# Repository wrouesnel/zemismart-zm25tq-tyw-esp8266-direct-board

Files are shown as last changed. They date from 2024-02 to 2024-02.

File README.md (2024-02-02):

# ESP8266 Adapter Board for Zemismart ZM25TQ-TYW Tubular Motor

This is a PCB I designed for doing an ESP chip swap on the Zemismart ZM25TQ-TYW tubular motor.

It allows a simple direct replacement of the WBR1 microcontroller board, which rides on a carrier shim to
mate with the motorized blind itself. Communication happens over serial using the Tuya protocol, so ESPHome
can speak to it easily.

The carrier board in the motor tube is marked `TYWBR1_VER 0.0 210131`. The PCB in this repository is
designed to be a direct replacement for it, carrying an ESP-07 or ESP-07S (ESP-07S recommended).

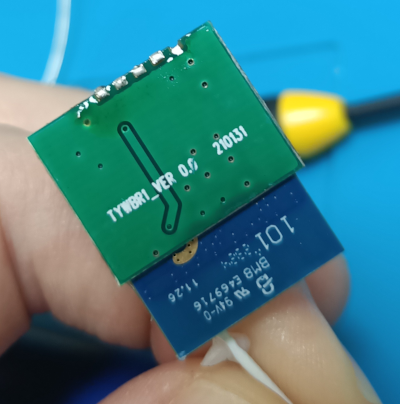
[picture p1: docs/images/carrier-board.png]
Carrier Board


You want to use the ESP-07 series because of the on-board SMA connector, which allows using the included antenna
with the tubular motor directly. You need to remove a 0 ohm resistor from these boards to use the external antenna.

The resistor to remove is shown below - the pads closest to the chip.

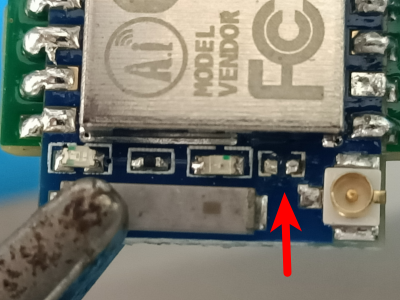
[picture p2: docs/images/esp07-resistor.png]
Desoldered Resistor


## Production

The [JLCPCB production files](jlcbpcb/production_files) I used for this board are included, use the SMD single-sided assembly service - all parts
are basic resistors which costs cents for assembly.

One consideration with production was I used the default PCB thickness - this worked fine, but a thinner PCB might
be better since castellate solder pads cost considerably more - and a little less height will help with the workaround
for soldering.

## Usage

**NOTE**: these instructions assume you know what you are doing. If this all seems to daunting, please don't plough
ahead anyway.

Make sure you flash your ESP with ESPHome before assembling everything! How to do this is described well elsewhere.
The ESPHome configuration to set the motor up as a [generic blind](esphome/generic-zemismart-zm25tq-tyw.yaml) is here.
I recommend customizing it for your use case (namely: set it up to auto-connect to your wifi, I've also added a required
secret for the fallback-wifi-password - you don't want that to default to open).

The motor comes apart fairly easily - just undo the screws (the design seems to have improved since the first one
I bought which required more force). I did have to desolder the reset switch to get it out. Take pictures while
you disassemble so you can re-assemble.

The image below shows the two boards side by side sitting on top of the blind motor board.

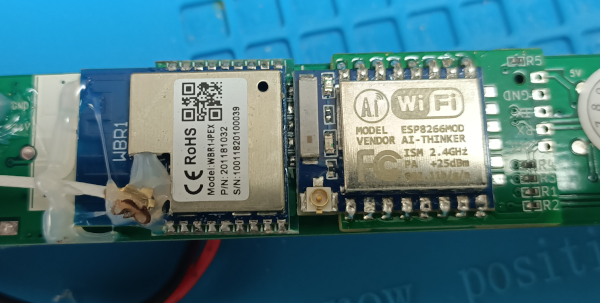
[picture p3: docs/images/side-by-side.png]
Side-By-Side


The easiest way to desolder this board is to add more solder to bridge all the pads, then use the soldering iron to
heat the blob up to liquid. There's tape underneath the chip, so use a small screw-driver to get the board up. Make
sure the solder is melted though - the traces underneath are fragile and can get lifted doing this (though there are
ways to repair it).

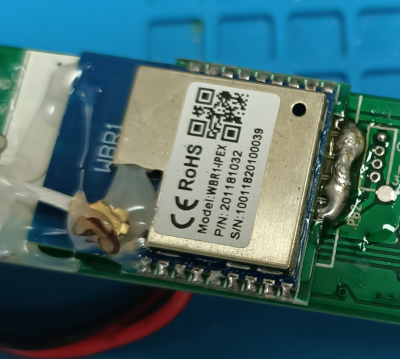
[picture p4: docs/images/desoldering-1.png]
Desoldering


Showing the chip and the tape...

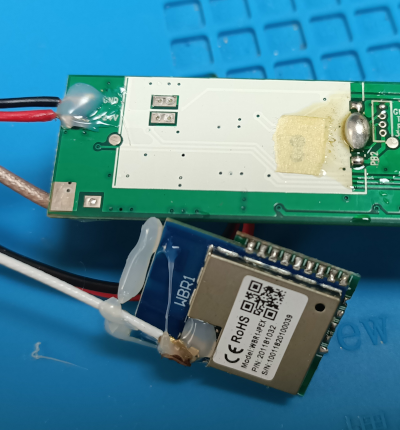
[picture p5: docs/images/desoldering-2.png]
Desoldered


Use a desoldering gun or some solder wick to clean up the pads. I have a cheap desoldering station which works great.

I put red electrical tape over the white section of the mask to cover the test pads - these have 24V when the motor
is powered, so it's just some extra insulation.

The PCB doesn't have castellate pads - they add a considerable premium. The two possible solutions are to file the pads
on the edge till the open up, or to do a kind of careful solder bridge over the edge. I opted for the latter, but it
is is tricky - try what works best (I'll try the pseudo-castellation next time round).

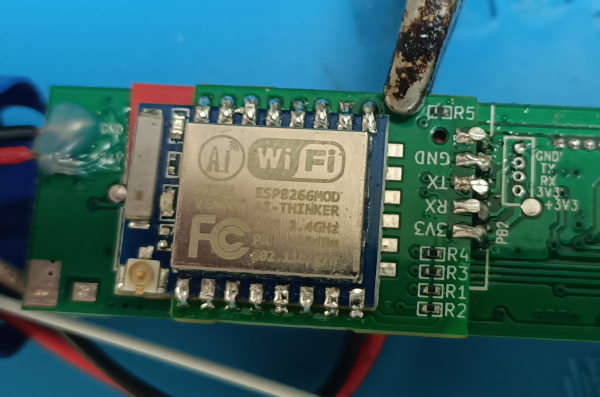
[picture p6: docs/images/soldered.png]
Soldered


The original PCB is hot glued down to provide support. I used electrical tape to cover the pseudo-castellations and the
top of the IPEX antenna. The final product looks like this, and fits back in the tube nicely.

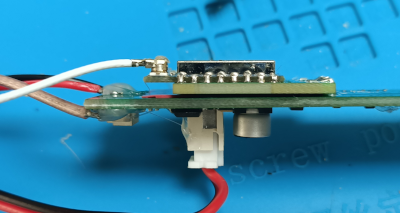
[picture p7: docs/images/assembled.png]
Assembled


And taped up:

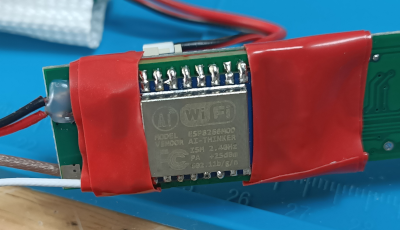
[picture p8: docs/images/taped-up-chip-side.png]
Chip Side
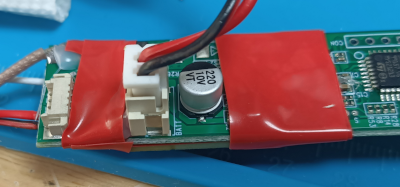
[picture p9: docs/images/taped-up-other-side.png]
Other Side
 

When it's all back together, it's seamless - but maybe put a label on it so you know it's been chip-swapped (also
which specifies the name of the chip you put in - there's a lot of options you could go with).

### Will it work elsewhere?

Probably! I suspect this carrier board is pretty common. The Zemismart motor design has been improved and disassembled
quite well, so having the carrier board in hand made swapping it out a breeze.

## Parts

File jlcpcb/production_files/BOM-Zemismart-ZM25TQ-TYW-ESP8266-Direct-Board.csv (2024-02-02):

Comment | Designator | Footprint | LCSC
10K | R1,R2,R3,R4,R5 | R0402 | C25744

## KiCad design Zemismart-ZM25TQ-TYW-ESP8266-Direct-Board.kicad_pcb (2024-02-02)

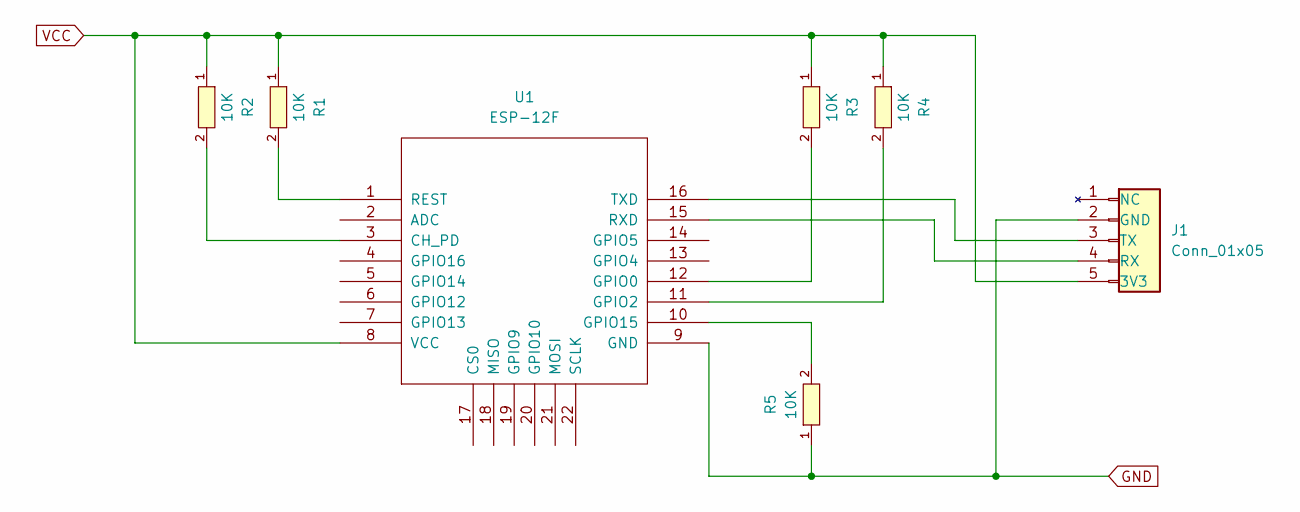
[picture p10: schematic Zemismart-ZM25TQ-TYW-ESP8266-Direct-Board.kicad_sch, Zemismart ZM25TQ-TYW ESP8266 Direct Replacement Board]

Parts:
J1: Conn_01x05; JST_PH_B5B-PH-K_1x05_P2.00mm_Vertical
R1, R2, R3, R4, R5: 10K; R0402; LCSC C25744
U1: ESP-12F; ESP-12E_SMD

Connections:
GND: J1.2 (GND), R5.1, U1.9 (GND)
unnamed: J1.4 (RX), U1.15 (RXD)
unnamed: J1.3 (TX), U1.16 (TXD)
unnamed: R2.2, U1.3 (CH_PD)
unnamed: R3.2, U1.12 (GPIO0)
unnamed: R4.2, U1.11 (GPIO2)
unnamed: R5.2, U1.10 (GPIO15)
unnamed: R1.2, U1.1 (REST)
VCC: J1.5 (3V3), R1.1, R2.1, R3.1, R4.1, U1.8 (VCC)

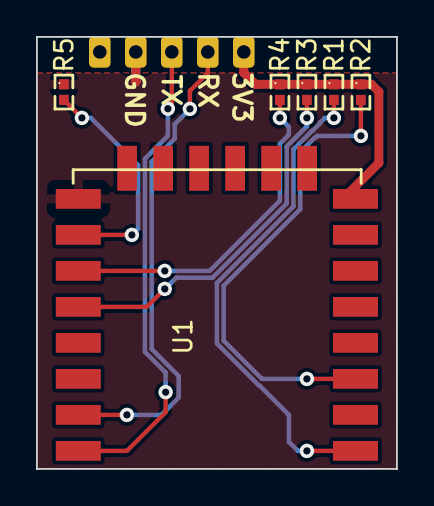
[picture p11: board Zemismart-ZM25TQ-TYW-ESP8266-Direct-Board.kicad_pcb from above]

Board: 2 copper layers, 20.0 x 24.0 mm, 7 parts (0 on the bottom side), 9 nets.

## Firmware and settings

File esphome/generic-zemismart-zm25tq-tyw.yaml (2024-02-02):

# ESP-1S chip-swapped Zemismart ZM25TQ (TY-W) motorized blinds.
# These have a WBR1-IPEX chip in them originally, communicating over
# serial. It provides 3.3V power and 3.3V TTL lines.

external_components:
- source:
    type: local
    path: components

esphome:
  name: cover-zemismart-blinds
  friendly_name: Zemismart ZM25TQ Blinds
  name_add_mac_suffix: true
  platform: ESP8266
  board: esp01_1m
  project:
    name: "wrouesnel.zemismart-zm25tq-esp01"
    version: "1.0"
  esp8266_restore_from_flash: false

logger:
  level: DEBUG
  baud_rate: 0

web_server:
  port: 80

captive_portal:

mdns:

api:

ota:

wifi:
  ap:
    password: !secret fallback_wifi_password

uart:
  tx_pin: TX
  rx_pin: RX
  baud_rate: 9600

tuya:

cover:
  - platform: tuya-ex
    name: Motor
    control_datapoint: 1
    position_datapoint: 2
    position_report_datapoint: 3
    restore_mode: NO_RESTORE
    min_value: 0
    max_value: 100
    device_class: blind
    invert_position_report: true

number:
  - platform: tuya
    name: Set Position
    min_value: 0
    max_value: 100
    step: 1
    number_datapoint: 2
    unit_of_measurement: "%"
    mode: box
    entity_category: DIAGNOSTIC

sensor:
  - platform: uptime
    name: Uptime
  - platform: wifi_signal
    name: WiFi Signal
    update_interval: 60s
    entity_category: DIAGNOSTIC
    # Sensors from Tuya
  - platform: "tuya"
    name: "Reported Position"
    sensor_datapoint: 3
    entity_category: DIAGNOSTIC
  # - platform: "tuya"
  #   name: "Setpoint Position"
  #   sensor_datapoint: 2
  #   entity_category: DIAGNOSTIC
  - platform: "tuya"
    name: "Current Operation"
    sensor_datapoint: 7
    entity_category: DIAGNOSTIC
  - platform: "tuya"
    name: "Current Situation"
    sensor_datapoint: 11
    entity_category: DIAGNOSTIC
  # Bitfield: 1 appears to mean "limits not set" - TODO: lock out the cover controls from HA
  # until limits are set.
  - platform: "tuya"
    name: "Motor Fault"
    sensor_datapoint: 12
    entity_category: DIAGNOSTIC

switch:
- platform: tuya
  name: Lower Limit Set
  switch_datapoint: 103
  entity_category: CONFIG
- platform: tuya
  name: Middle Set
  switch_datapoint: 104
  entity_category: CONFIG
- platform: tuya
  name: Upper Limit Set
  switch_datapoint: 105
  entity_category: CONFIG

select:
- platform: tuya
  name: Motor Direction
  enum_datapoint: 5
  options:
    0: Normal
    1: Invert
  entity_category: CONFIG
- platform: tuya
  name: Motor Mode
  enum_datapoint: 106
  options:
    0: Continuous
    1: Stepped
  entity_category: CONFIG

text_sensor:
  - platform: version
    name: ESPHome Version
    entity_category: DIAGNOSTIC
  - platform: wifi_info
    ip_address:
      name: IP
    ssid:
      name: SSID
    bssid:
      name: BSSID
  
